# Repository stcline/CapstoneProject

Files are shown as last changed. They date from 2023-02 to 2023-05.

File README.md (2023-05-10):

# Capstone - Sentury Turret
Robotics Engineering Capstone Project

Brady Sanger and Camden Timmons

May 10, 2023



## Design Summmary

Untitled drawing

Untitled drawing (2)

Our device is an automated turret that can sense someone and turn to shoot them. When turning the system on, you must first enter a distance on the number pad. This distance is how far the sensor is from the point of rotation, or, in other words, the center of the pyramid. This distance is later used for some simple trigonometry. After doing this, the turret will start working. If you walk in front of the distance sensor, it will take the distance you are away from the sensor as well as the input distance you entered earlier to find the centeral angle. In order to find the centeral angle, we use the inverse tangent or arc tangent.

The equation looks something like:

**arctan(Sensed Distance/Inputted Distance) = Centeral Angle in Radians**

A diagram of how it works can be seen in **Figure 1**. 

That is all the basic angle finding, but what about the rest? Using the angle we get above, we turn a servo to that angle, this should turn the actual turret part toward the target. Then we start spinning the flywheel on the turret (two really fast wheels) in opposite directions so that when we feed through a nerf dart, it can shoot the dart. Using another servo, we push the pre-loaded dart forward into the flywheel, propelling it forward.

Refer to **Figure 2** to see a flowchart of how our project works. 

## System Details

 Many parts of this project were manufactured using a 3D printer, and with so many unique parts, you may want to know what they are and what they do! 

### Flywheel

The flywheel is a simple device that simply has two motors that spin wheels. When the nerf dart is pushed into these wheels, it is propelled forward. This system is very similar to the real nerf flywheels used in some nerf guns.  **Figure 3** shows a visual of the flywheel design. 

### Magazine

The magazine is what holds the nerf darts as well as pushes the darts into the flywheel. This piece is directly mounted to the flywheel. Using one servo, a custom-designed servo horn, a very long 35mm 3M screw, and a hex nut, we are able to push the dart forward into the fly wheel. There is a guide rail in the design that is shorter than all the other openings Refer to **Figure 4**.

### Pyramid and Base

The pyramid and base are used to mount the flywheel and magazine as well as hide some of the wires and the Arduino Mega used for this project. Here is where we put the motor controller, battery pack, Arduino Mega, and the turning servo. Here we also have mounted the number pad and the off and on switch. Here we also have our LEDs that tell you what's happening. **Figure 5** shows the pyramid and base. 

### Circuit Schematic

With all these different servos, motors, controllers, etc., we need a diagram to see the wiring! Here you can see the pins everything is connected to and where it goes.

**Figure 14** shows the circuit diagram.

### Software Diagram

**Figure 7** shows a diagram to show what the Arduino is thinking throughout the entire process after you turn the turret on. They keypad was also a major device we had to learn how to use, as can be seen in **Figure 15**.

## Design Evaluation

For this capstone, there were many requirements you had to meet to get a good grade. Here are the various categories and how we think we did. 
 
### Output Display

For our output, we used two LEDs that show if you have entered the numbers on the number pad, if you pressed A on the number pad to start normal operation, and if a target is sensed. We think we hit this requirement fairly well, but we didn't use any very complex parts, so we think we did hit this category, but it can be approved.

### Manual User Input

For this, we used a keypad, which is overall fairly difficult to use. Using this, with it also effecting the entire system as well as being shown on the LEDs, we think we hit this category well. We think this could be approved, however, if we created a manual mode as well as a sentry mode.

### Automatic Sensor

For our automatic sensor, we used a supersonic distance sensor, which uses sound to find distance. We think we hit this category well, and because of how important this single sensor is to the entire system, we think we hit this requirement fairly well.

### Actuators, Mechanisms, and Hardware

Here, we used many different actuators. Our project used two micro servos as well as two DC motors. They are all vital parts of our project. We also had a cleverly designed mechanism for pushing the nerf darts. We think we hit this right on the dot and that we did very well here.

### Logic, Processing, and Control

We have a lot of code for this project. We are also using many libraries effectively to simplify our code. In our code, we also have some hard calculations, such as finding the centeral angle using arctangent, which seemed to be very difficult for the Arduino to understand. We think we did fairly well here, not only in making simple, concise code but also in using various hard calculations.

### Other adjustments

There were also many other adjustments that could positively or negatively affect your grade. Here we will mention only things I think we did well or badly, but nothing we don't think will affect us.

Construction, Quality, Aesthetics, and Visual Appeal

We think we will get extra points here, however we think we could stay nuetral here. Our project overall looks good with almost everything hiding inside besides for things that must absolutely stick out.

Level of Effort

We think we will get extra points here, because we put in a lot of effort to get this project running including many hours of out of class work and designing for many parts of this project.

Cost

We are almost certain we will get this because our project as a total cost between only 40 and 50 dollars which seems to be the lowest in the class.

## Lessons Learned

We learned many lessons on this project, but most of all patience. So many parts of this projuct simply required waiting or very slow progress through a proplem.

One difficult problem we encountered was the magazine design as well as pushing the darts. We went through many different designs and iterations of our magazine to try and let it hold bullets while also pushing them, and for whatever pushing them to not be in the way of the bullet. Originally we had guide rails on the magazine and a servo would slide a special pusher design through the guide. This solution however didn't work because there was too much friction of the plastics on eachother and it couldn't glide through. Our solution was to use a screw and a hex nut mounted to our special servo horn that could slide through the guide rail while also staying straight.

We also learned lessons in work time usage. Pushing a large project twords the end even when it isn't your fault can still majorly effect your time usage and your priorites. Our project got largly delayed by sickness as well as shipping and broken parts leading to us having to rush tword the end. This is a bad method and I'd recommend more planning before entering a large project like this.

## Parts List

- 2 Motors (CHECK WITH CLINE)
- 2 Tower Pro Micro Servo 99, SG90 (Can be found on Amazon) $15.95 Model Num: SG90A2
- 1 Songhe 4 x 4 Matrix Array Membrane Switch Keypad Keyboard (Can be found on Amazon) $1.80 Model Num: Keyboard
- 1 Gikfun MTS102 2 Position 3 Pins Mini Toggle Switch (Can be found on Amazon) $0.90 Model Num: LYSB01BWL7Z44-ELECTRNCS
- 1 Elegoo Arduino Mega 2560 (Can be found on Amazon) $20 Model Num: EL-CB-003
- 1 Qunqi L298N Motor Driver (Can be found on Amazon) $4 Model Num: MK-050-2
- 1 Qunqi 400 tie Point Experiment Mini Breadboard (Can be found on Amazon) $6 Model Num: 8541770369
- OWOFYDR 100 pcs 5mm Green LED Diode Lights (Only need 2 out of 100, Can be found on Amazon) $0.14 per LED, 7 per pack Model Num:OWO-LED-1008
- REV 35 mm Screw (REV Robotics online store) $0.23 for one, 11.50 for pack Model Num: REV-41-1125-PK50 
- REV M3 nut (REV Robotics online store) $0.055 for one, 5.50 for pack Model Num: REV-41-1126-PK100

### Non-Specific Parts

- Solder
- Soldering Iron
- Hot glue
- Hot glue gun
- Wires
- Wire
- Wire cutters
- Shrink Wrap / Electrical Tape
- Heat Gun (If using shrink wrap)
- Drill
- 3D printer
- Wire Nuts
- Lot's or patience
- 9v Power Source

## Instructions on how to make it

First off, print all of the parts in the CAD file. This should take a while, but it is all needed. We recommend using ABS or likewise filiments like ASA. The only part that needs to be duplicated is the wheel, we need two of those. Depending on your 3D printers limitations you may need supports on some places and not others.

### Flywheel

Lets make the flywheel!

This part is kind of hard so pay attention. 

First lets get the motors mounted. This part is kind of awkward so you may need a helping hand. You need to hold the motors in the holes at the top of the flywheel frame so that it barely pokes out. Then hot glue this down. Repeat this on the other side. Refer to **Figure 3** to see how it should look.

Now the wheels are friction fit so it will be hard to put those on. Just push them on so that the side with the extra nub is pointing down. Refer to the image above. At this point I recommend making sure that when you push through nerf darts they actually contact the wheels. If they do then we can move on! If not you may need to re-glue the motors.

Now you need to solder wires to the little tabs on the motors. Simply solder any wire on and try not to bend the tabs because they are very fragile. 

Now let's add the magazine. You simply need to glue this peice on to the rail the nerf dart and lay in. You can see where on **Figure 8**

Now here is where we got droven crazy. You need to put your servo horn on your servo and fish it into the casing on the mag so that the horn is facing down. Now you need to turn the servo horn in a way so that you can put a screw in it, however you do not want it to enter the actual mag yet. Now slowly start turning the hex nut up the servo horn and then place it in the guide rail as seen in **Figure 9**.

Then lift the screw and place it in the guide rail. Slowly tighten the nut until the nut and screw head are both nearly touching the servo horn. It should look like **Figure 10**.

## Wiring

Now using the wiring diagram shown above you need to wire everything together. It's gonna suck, but trust me it will be worth it. This will probably be most of your time though. **Figure 11** and **12** show a couple photo's of the internals.

This should give a general idea on how to lay it out however feel free to customize placements.

Here you can also mount the turnS servo that connects to pin 4. This should be mounted to the top of the pyramid.
Also put the number pad on the outside and drill a hole next to it for you to put your switch. Refer to **Figure 13**

Now all you have left is to place the flywheel on the top of the turnS servo. We recommend to fill the hole for mounting with hot glue and the putting it on. Once doing this and then wiring it up your all done!

## Appendix
**Figure 1 (Equation diagram)**
Trig (1)

**Figure 2 (Flowchart)**

Screenshot 2023-05-05 8 45 22 AM

**Figure 3 (Flywheel)**


**Figure 4 (Magazine)**


**Figure 5 (Pyramid and Base)**


**Figure 7 (Software diagram)**

W 

**Figure 8 (Magazine Placement)**


**Figure 9 (Servo Horn Placement)**


**Figure 10 (Screw Placemen)**
  

**Figure 11 (Wiring pt. 1)**


**Figure 12 (Wiring pt. 2)**


**Figure 13 (Pyramid and Number Pad)**


**Figure 14 (Circuit Diagram)**


**Figure 15 (Keypad Code)**
```
void getNumbers()
{ 
  // Checks if there is a custom key entered
  char customKey=customKeypad.getKey();
  // If there is then it continues
  if (customKey){
    // If custom key isn't A than add it to the variable enteredNums
    if (customKey != 'A'){
      enteredNums = enteredNums+customKey;
      // To turn on the LEDS
      if (l1ON == false){
        digitalWrite(led1, HIGH);
        l1ON = true;
      }
      else{
        digitalWrite(led2, HIGH);
      }
    }
    // If the button pressed is A than turn entered nums into an interger, and adjust lights
    if (customKey == 'A'){
      x = enteredNums.toInt();
      enterNums = true;
      l1ON = false;
      digitalWrite(led1, LOW);
      digitalWrite(led2, LOW);
    }
  }
  
}

```

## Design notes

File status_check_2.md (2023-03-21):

So far in our project we have used Arduino Web Editor, OnShape, and a variety of learning on sensors from many sites. One major site we have used is 
arduinomodules to learn how sensors work and get basic code for them. We as of now don't need to purchase any parts, however when it comes to manufactuing
we still need to work on our fly wheel system that shoots the bullets and refine it. We also need a housing to contain our parts such as the Arduino as well 
as places for the ultrasonic sensors. We also got a LED turning on and off with a IR reciever and a IR remote. This will be helpful for giving commands.

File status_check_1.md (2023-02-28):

Which parts of the project have you begun constructing to get to the final working solution?

We have began doing CAD for our project creating the fly wheel needed to shoot the nerf darts. We also have some of the simple electronics and sensors
coded.

Have you ordered all additional parts that will be needed?  When will they arrive if they have not already?

We don't need additonal parts that are ordered. All the parts we need are in the lab.

Have you designed any of the parts that will need to be manufactured?  If not, when will those designs be done?

We have started creating the fly wheel to shoot the nerf darts. We still need to design the parts that hold the components (the outer shell).

If you are able to complete the project by May 13th to your expectations, will you receive full credit in all five functional element categoriesLinks to an external site. (list how you meet each requirement)?

We should be able to meet all the requirments. Output display - RGB LED, LCD  Manual User Input - Remote system (Joystick, Button)  Automatic Sensors - UltraSonic Sensors, Actuator - Servo, Motor Logic - Programmed

What are the three most significant design challenges you foresee for this project?

The significant design challenges are the CAD shell, the shooting mechanism, and getting all the sensors to follow someone who is moving.

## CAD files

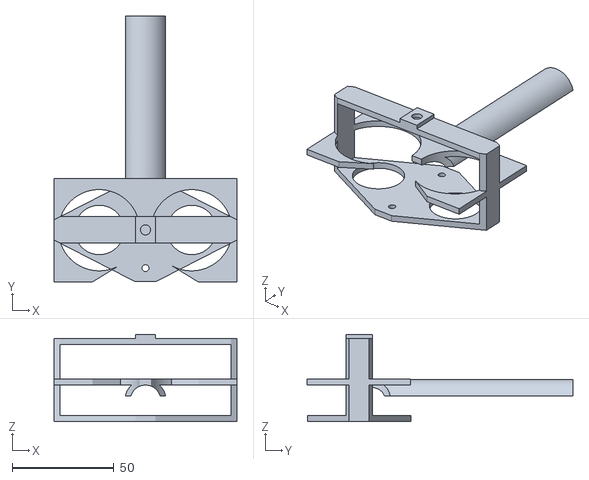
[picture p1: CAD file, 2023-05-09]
CAD/Plate (3).stl
90.0 x 131.0 x 43.0

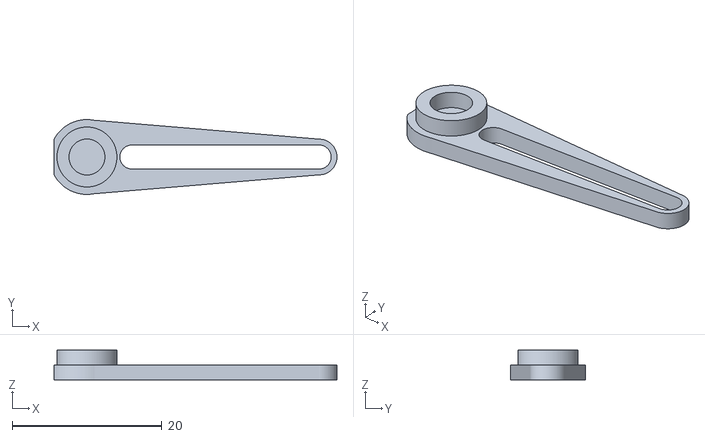
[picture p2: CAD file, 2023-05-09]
CAD/Horn.stl
37.8 x 10.00 x 4.00

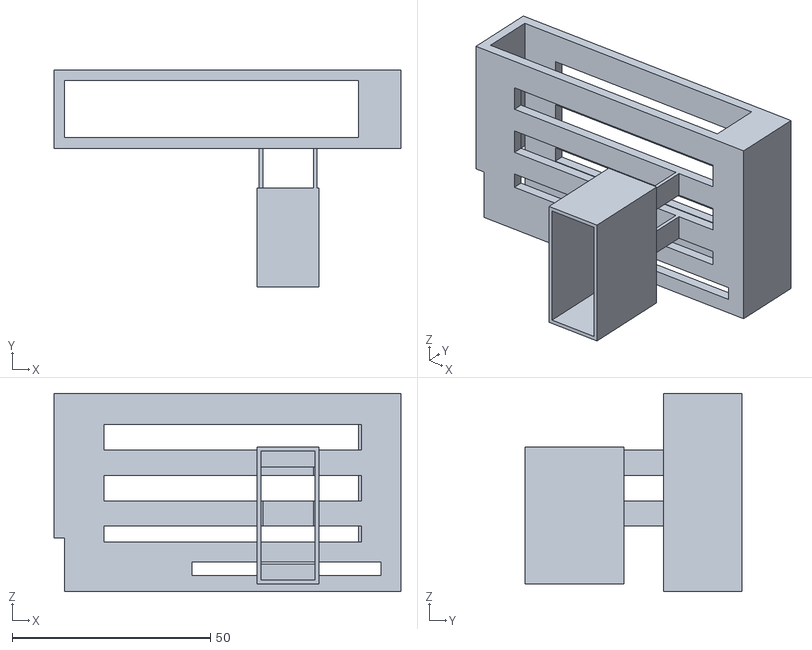
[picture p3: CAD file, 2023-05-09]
CAD/Mag.stl
87.6 x 54.9 x 50.0

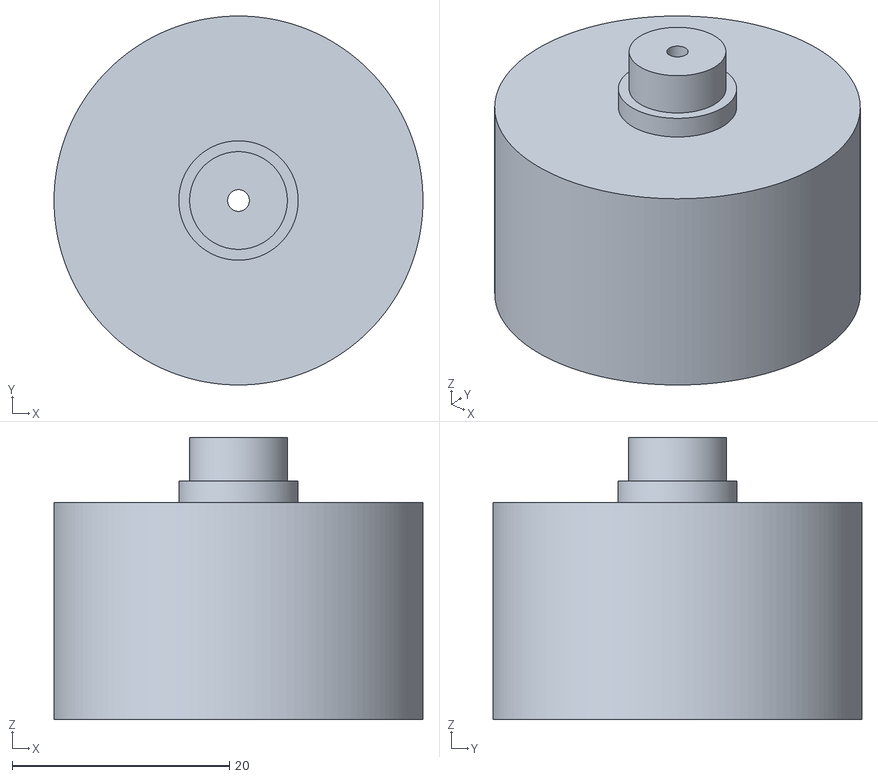
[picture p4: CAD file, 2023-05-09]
CAD/Wheel (4).stl
34.0 x 34.0 x 26.0

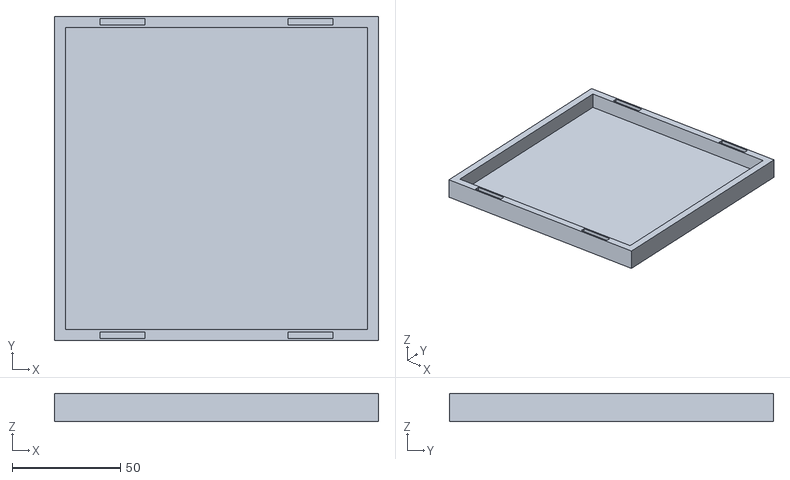
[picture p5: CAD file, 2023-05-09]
CAD/BASE (1).stl
150.0 x 150.0 x 13.0

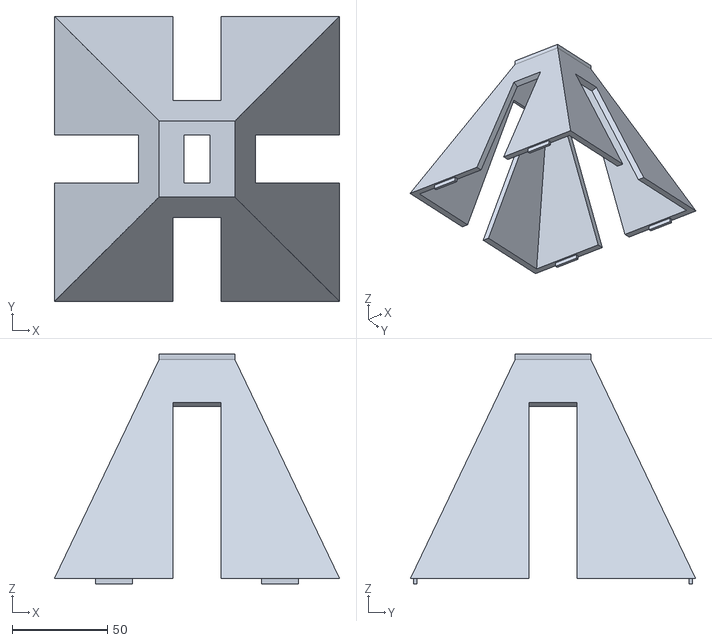
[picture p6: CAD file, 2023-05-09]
CAD/PYRAMID.stl
150.0 x 150.0 x 121.0

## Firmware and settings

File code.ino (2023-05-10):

// Include Libraries
#include <Servo.h>
#include <Keypad.h>
// Define pins for distance sensor
#define trigPin1 13
#define echoPin1 50
#define led1 36 
#define led2 35
// define global variables
long sduration1;
float sdistance1;
bool movement;
bool enterNums;
bool l1ON;
String enteredNums;
// Inputed value from NumPad
int x;
// Angle for turnS servo
float angle;
const byte ROWS = 4; //four rows
const byte COLS = 4; //four columns
// Setting up servos
Servo turnS;
Servo shootS;
// Motor Controller variables
int ena=6;
int in1=32;
int in2=33;
//define the symbols on the buttons of the keypads
char hexaKeys[ROWS][COLS] = {
  {'1','2','3','A'},
  {'4','5','6','B'},
  {'7','8','9','C'},
  {'*','0','#','D'}
};
byte rowPins[ROWS] = {22, 23, 24, 25}; //connect to the row pinouts of the keypad
byte colPins[COLS] = {26, 27, 28, 29}; //connect to the column pinouts of the keypad
//initialize an instance of class NewKeypad
Keypad customKeypad = Keypad( makeKeymap(hexaKeys), rowPins, colPins, ROWS, COLS); 
void setup()
{
// Making sure bool is false
movement = false;
Serial.begin (9600);
// PinModes
pinMode(trigPin1, OUTPUT);
pinMode(echoPin1, INPUT);
pinMode(ena, OUTPUT);
pinMode(in1, OUTPUT);
pinMode(in2, OUTPUT);
pinMode(led1, OUTPUT);
pinMode(led2, OUTPUT);
// Attaching servos to pins
turnS.attach(4);
shootS.attach(5);
// Use Ultrasonic Sensor start run
// This gets the sdistance used later
delay(100);
digitalWrite(trigPin1, LOW);
delayMicroseconds(2);
digitalWrite(trigPin1, HIGH);
delayMicroseconds(10);
digitalWrite(trigPin1, LOW);
sduration1 = pulseIn(echoPin1, HIGH);

// Calculate distance
sdistance1 = sduration1* 0.034 / 2;
// Confirming bool is false
enterNums = false;
l1ON = false;
// Draw back mag servo
shootS.write(35);
}

void loop() {
// Define kind of variables
long duration1, duration2;
float distance1, distance2;

// Use Ultrasonic Sensor
digitalWrite(trigPin1, LOW);
delayMicroseconds(2);
digitalWrite(trigPin1, HIGH);
delayMicroseconds(10);
digitalWrite(trigPin1, LOW);
duration1 = pulseIn(echoPin1, HIGH);

// Calculate distance
distance1 = duration1 * 0.034 / 2;
// Delay to not overload arduino
delay(200);
// Testing to see if numbers on numpad have been entered
if (enterNums == false){
  getNumbers();
}
// If numbers have been entered then it getDirection below, if that true it used the function to shoot 
if (enterNums == true) {
  getDirection(distance1, sdistance1, x);
  if (movement == true) {
    shootEmJohn(angle);
  }
  delay(100);
}
}
// Used to find the difference between the original distance and what it sensed now
void getDirection(int d1, int s1, int x)
{
  if ((d1 < (s1-10)))
  {
  //Serial.println("TARGET"); //These are all testing prints that are useful if you don't know if it's working
  //Serial.println(d1);
  //Serial.println(x);
  //Uses arc tangent to calculate centeral angle, more on the README.md 
  angle = atan2(d1,x);
  // Turns radian mesure to degrees
  angle=angle*(180/3.14159);
  movement=true;
  }
}
void getNumbers()
{ 
  // Checks if there is a custom key entered
  char customKey=customKeypad.getKey();
  // If there is then it continues
  if (customKey){
    // If custom key isn't A than add it to the variable enteredNums
    if (customKey != 'A'){
      enteredNums = enteredNums+customKey;
      // To turn on the LEDS
      if (l1ON == false){
        digitalWrite(led1, HIGH);
        l1ON = true;
      }
      else{
        digitalWrite(led2, HIGH);
      }
    }
    // If the button pressed is A than turn entered nums into an interger, and adjust lights
    if (customKey == 'A'){
      x = enteredNums.toInt();
      enterNums = true;
      l1ON = false;
      digitalWrite(led1, LOW);
      digitalWrite(led2, LOW);
    }
  }
  
}
void shootEmJohn(int a)
{
  //Turn servo
  turnS.write(a);
  //Start motors
  digitalWrite(in1, HIGH);
  digitalWrite(in2, LOW);
  analogWrite(ena, 255);
  delay(1000);
  //Push dart
  shootS.write(160);
  delay(1000);
  //Return to original position
  turnS.write(90);
  shootS.write(35);
  analogWrite(ena,0);
  movement=false;  
}

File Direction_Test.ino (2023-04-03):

//Pins used: 2345,54329876//Change some pins

// Include Libraries
#include <Servo.h>
#include <Keypad.h>


// Define pins for distance sensors
#define trigPin1 3
#define echoPin1 2
#define trigPin2 4
#define echoPin2 5

// define global variables
long sduration1, sduration2;
float sdistance1, sdistance2;
bool movementL, movementR;
bool enterNums;
char enteredNums;
int x;
int angle;
const byte ROWS = 4; //four rows
const byte COLS = 4; //four columns
//define the cymbols on the buttons of the keypads
char hexaKeys[ROWS][COLS] = {
  {'1','2','3','A'},
  {'4','5','6','B'},
  {'7','8','9','C'},
  {'*','0','#','D'}
};
byte rowPins[ROWS] = {9, 8, 7, 6}; //connect to the row pinouts of the keypad
byte colPins[COLS] = {5, 4, 3, 2}; //connect to the column pinouts of the keypad

//initialize an instance of class NewKeypad
Keypad customKeypad = Keypad( makeKeymap(hexaKeys), rowPins, colPins, ROWS, COLS); 

void setup()
{

Serial.begin (9600);
// PinModes
pinMode(trigPin1, OUTPUT);
pinMode(echoPin1, INPUT);
pinMode(trigPin2, OUTPUT);
pinMode(echoPin2, INPUT);
// Get Starting Positions


// Use Ultrasonic Left
digitalWrite(trigPin1, LOW);
delayMicroseconds(2);
digitalWrite(trigPin1, HIGH);
delayMicroseconds(10);
digitalWrite(trigPin1, LOW);
sduration1 = pulseIn(echoPin1, HIGH);
// Use Ultrasonic Right
digitalWrite(trigPin2, LOW);
delayMicroseconds(2);
digitalWrite(trigPin2, HIGH);
delayMicroseconds(10);
digitalWrite(trigPin2, LOW);
sduration2 = pulseIn(echoPin2, HIGH);
// Calculate distance
sdistance1 = sduration1 * 0.034 / 2;
sdistance2 = sduration2 * 0.034 / 2;
enterNums = false;
}

void loop() {
// Define kind of variables
long duration1, duration2;
float distance1, distance2;

// Use Ultrasonic Left
digitalWrite(trigPin1, LOW);
delayMicroseconds(2);
digitalWrite(trigPin1, HIGH);
delayMicroseconds(10);
digitalWrite(trigPin1, LOW);
duration1 = pulseIn(echoPin1, HIGH);
// Use Ultrasonic Right
digitalWrite(trigPin2, LOW);
delayMicroseconds(2);
digitalWrite(trigPin2, HIGH);
delayMicroseconds(10);
digitalWrite(trigPin2, LOW);
duration2 = pulseIn(echoPin2, HIGH);
// Calculate distance
distance1 = duration1 * 0.034 / 2;
distance2 = duration2 * 0.034 / 2;

// Test print
if (enterNums == false){
  getNumbers();
}
if (enterNums == true) {
  getDirection(distance1, distance2, sdistance1, sdistance2);
  delay(100);
}
}
// Test print function
void testPrintDist(int dist1, int dist2)
{
  Serial.print(dist2);
  Serial.print(" - ");
  Serial.print(dist1);
  Serial.println("");
}
void getDirection(int d1, int d2, int s1, int s2)
{
  int angle1;
  if ((d1 < (s1-7)))
  {
    Serial.println("LEFT");
    angle1=atan(d1/x);
    angle=angle1*(180/3.14159)
  }
  if ((d2 < (s2-7)))
  {
    Serial.println("RIGHT");
    angle1=atan(d2/x);
    angle=angle1*(180/3.14159)


  }
  
}
void getNumbers()
{
  char customKey=customKeypad.getKey();
  if (customKey){
    if (customKey != 'A'){
      enteredNums = enteredNums+customKey;

    }
    if (customKey == 'A'){
      x = int(enteredNums);
      enterNums = true;
    }
  }
  
}
